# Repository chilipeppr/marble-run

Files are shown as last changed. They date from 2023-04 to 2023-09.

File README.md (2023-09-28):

# Liberty Christian School - Strive Center - Evolving Marble Run

Author: John Lauer

<i>This project was donated to the Liberty Christian School to inspire the kids to embrace today's modern tools to innovate for our future.</i>

This repo contains the following items:
- <b>Fusion 360 Marble Run Design</b> - The 3D design of the Marble Run that hangs on the wall
- <b>Fusion 360 PCB Board Design</b> - The 3D electronics design of the PCB that drives the Marble Run
- <b>3D Printer 3MF Files</b> - The 3MF 3D printable files for all of the parts

# Fusion 360 Marble Run Design

<table>
<tr><td>
The Marble Run hangs on a wall that is at least 8' high, although you could adjust the height in 80mm increments 
by just reducing how many "scoops" are on the GT2 timing belt. 

The main parts of this design are:
- The top NEMA 23 stepper motor with GT2 timing belt gear and "popper outer" component that pops the marbles off the scoops and onto the track
- The bottom idler pulley, marble reservoir, agitator (to ensure marbles fill the loading pipe), and the loading pipe to the scoops.
- Track components including straight rails and 90 degree corner angle rails.

The idea for the Marble Run is to inspire the kids to print their own section of track, using any design they dream up, to contribute to getting the marble to roll all the way from the top of the elevator back to the reservoir at the bottom. This will requires hundreds of sections of track to loop around a column in the STEM lab. Kids will learn how to use CAD to design their track and how to 3D print.

You can view the Fusion 360 design in the Autodesk gallery online. https://a360.co/3HKXjhC

To print all of the parts of the Marble Run, you can view the Fusion 360 design and export each body as a 3MF. A directory of 3MF's is also made available in this repo.
</td>
<td width="200">
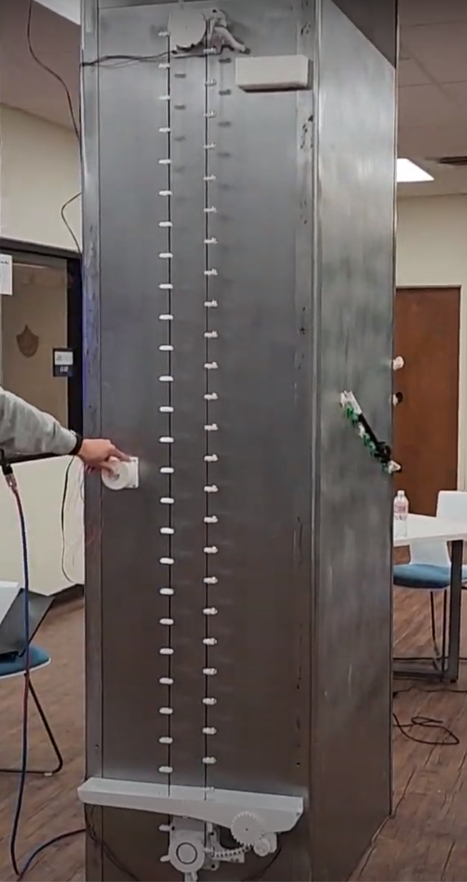
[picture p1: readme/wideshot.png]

</td>
</tr>
</table>

# Fusion 360 PCB Board Design

This is the driver board for the Marble Run. It has the following main modules:
- ESP32-S2 (Lolin S2 Mini)
- Stepper Motor TMC2209 Driver for Elevator
- Stepper Motor TMC2209 Driver for Agitator
- 2.42" OLED Display
- 24V to 5V DC to DC Converter
- 24V to 3.3V DC to DC Converter (Should have instead used AMS1117-3.3v off 5v bus)
- 24V Fan MOSFET Driver
- 24V Fan

You can view the board online in the Autodesk Gallery.
https://a360.co/3p5fhET

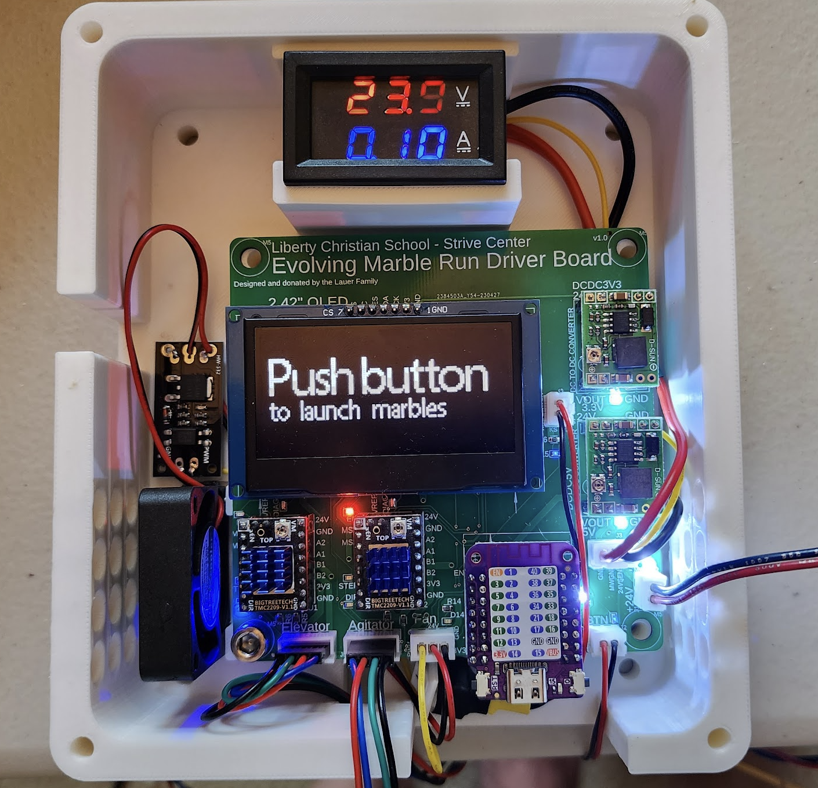
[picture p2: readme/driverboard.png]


This is a screenshot of what the PCB looks like inside Fusion 360.

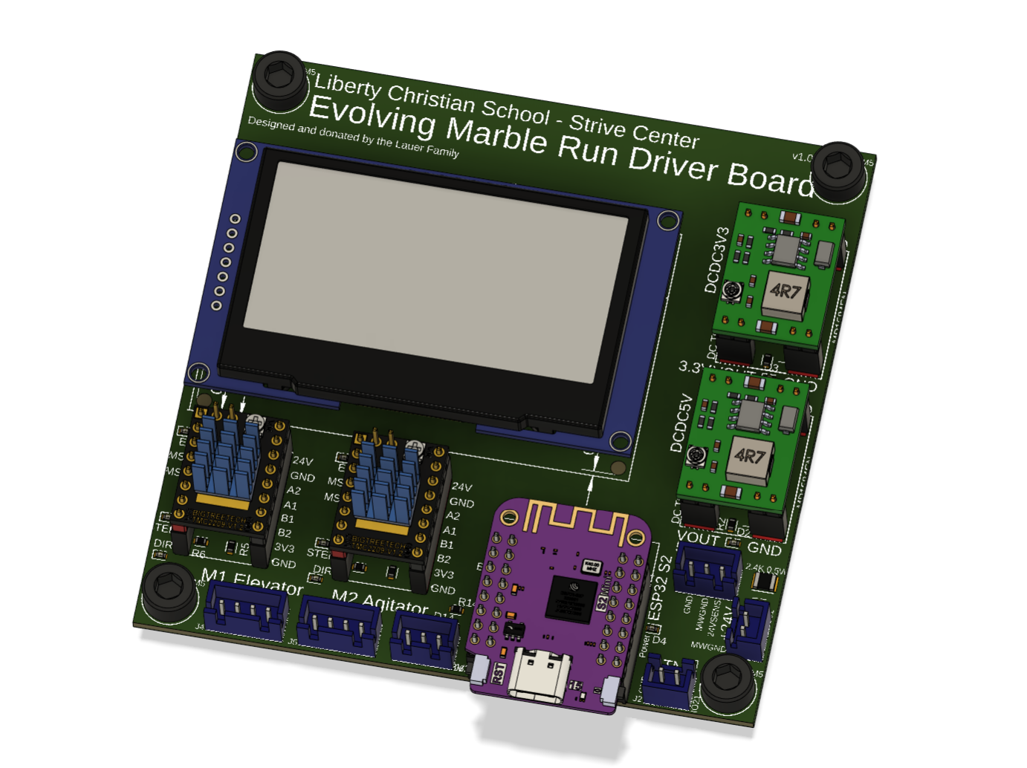
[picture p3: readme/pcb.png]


This is a preview of the board when ordering from JLCPCB including its placed components from their parts library.

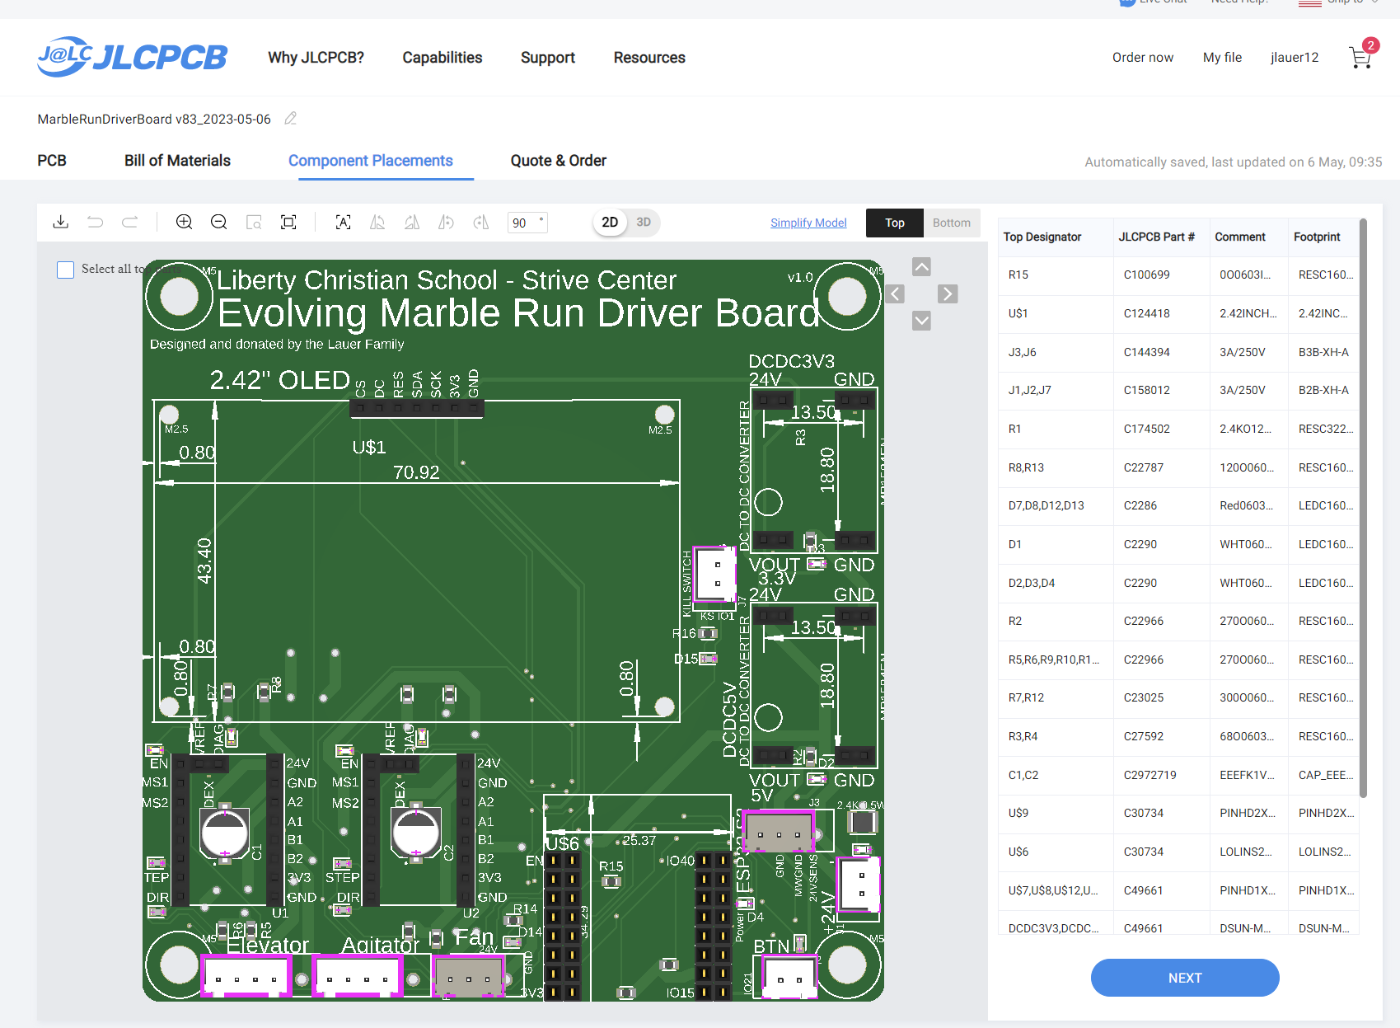
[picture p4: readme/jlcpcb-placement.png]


Here is a cost summary of the board.

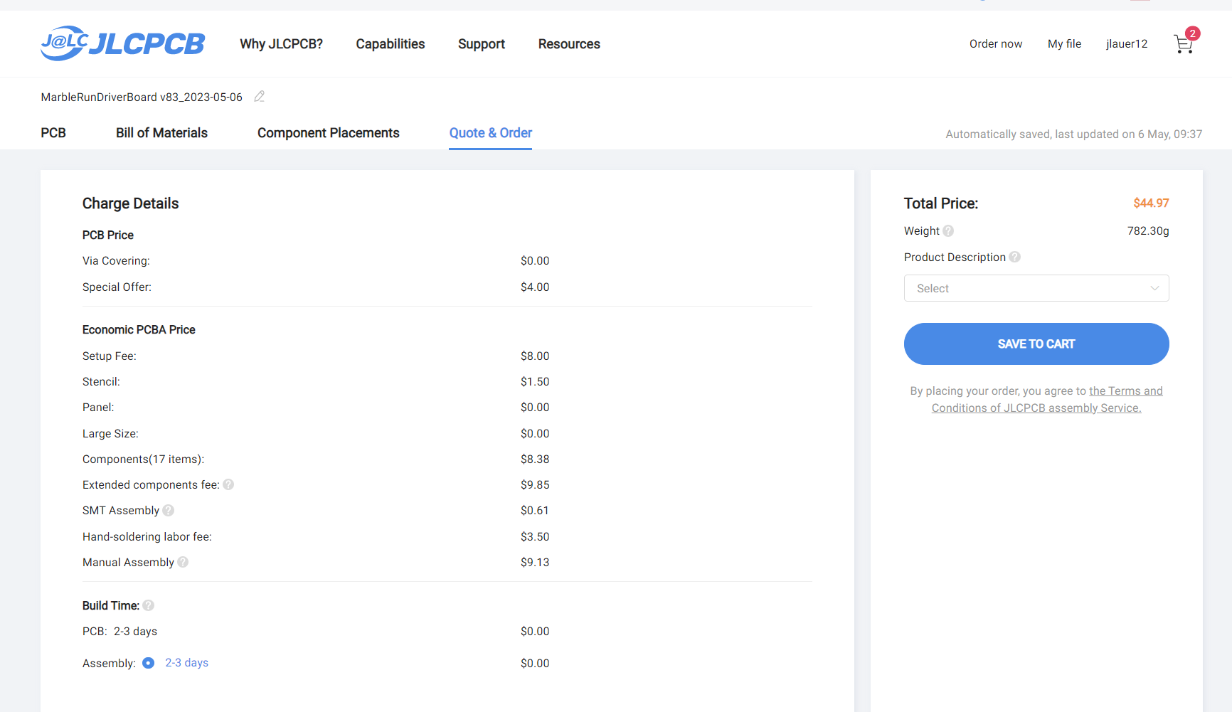
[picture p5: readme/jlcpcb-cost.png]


The code for running on an ESP32-S2 to control the Liberty Christian School Evolving Marble Run is available
in the "circuitpython 8.1.0 code" directory.

This is the board mocked up on a breadboard first before creating the final PCB.

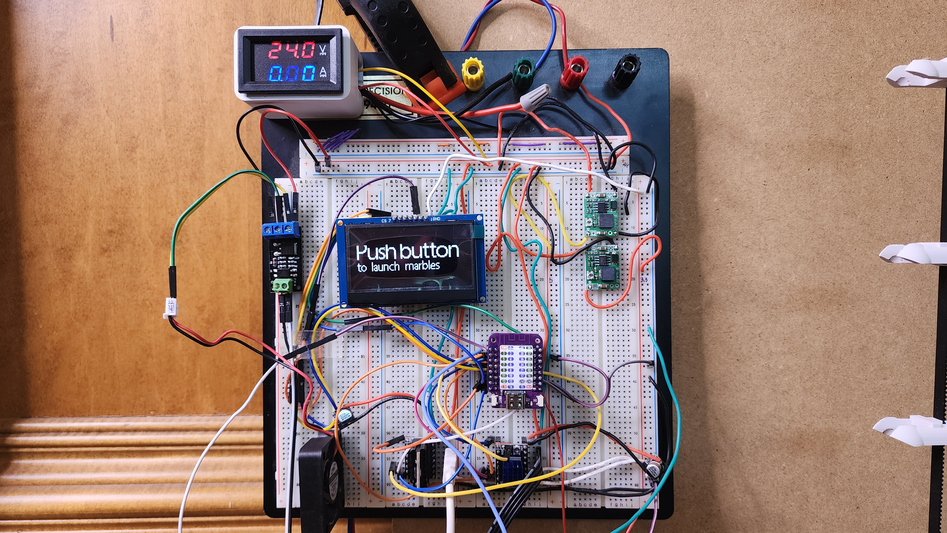
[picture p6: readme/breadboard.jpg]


# Schematic



















# Details of the Marble Run Components

This is a full view of the 8 foot tall Marble Run elevator that carries marbles from the bottom reservoir to the top of the run. This was mocked up prior to installing in the lab.

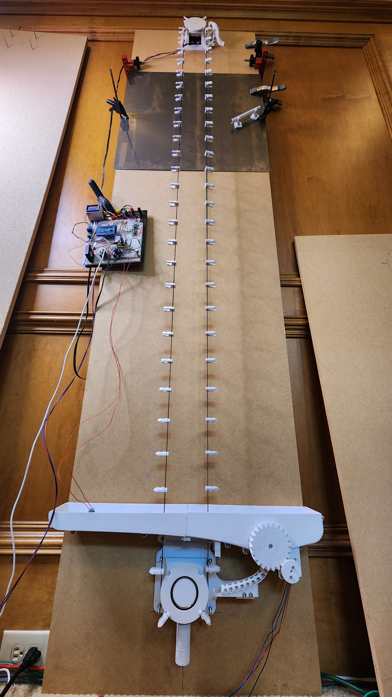
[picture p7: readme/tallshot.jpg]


This is a 3D rendering of the Marble Run. It was designed in CAD first to get all of the parts correct.

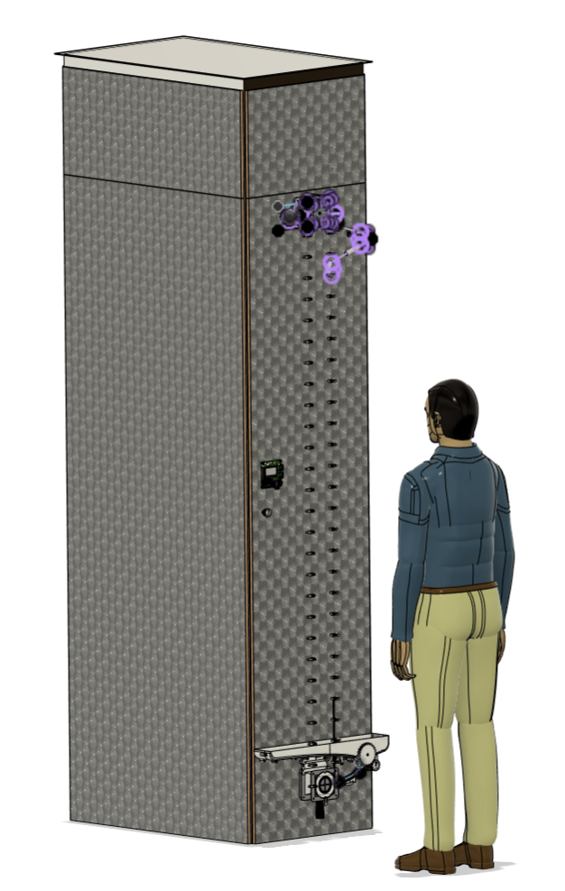
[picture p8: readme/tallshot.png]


This is the bottom reservoir. It has an agitator to ensure marbles are continuallyl flowing into the exit pipe, thus
ensuring the elevator is constantly picking up a new marble.

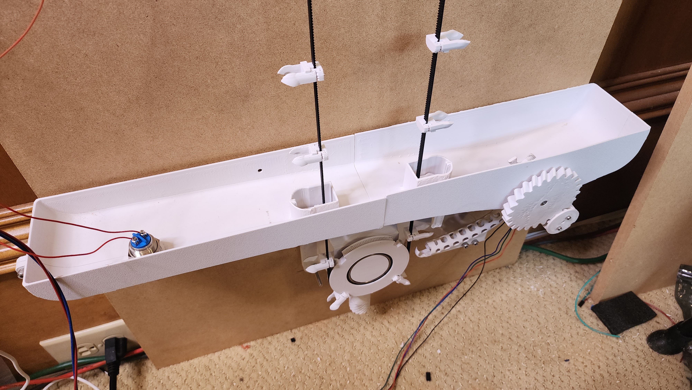
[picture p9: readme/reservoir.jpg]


This is the 3D rendering of the bottom reservoir.

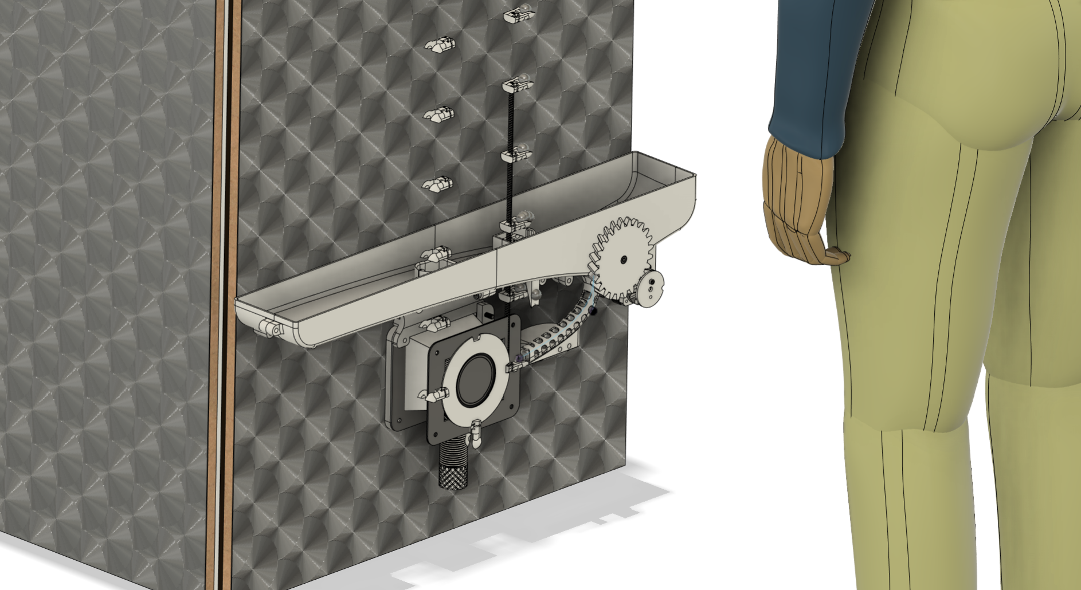
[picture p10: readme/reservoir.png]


This is the motor at top which rotates the GT2 timing belt. It is a NEMA 23 stepper motor.

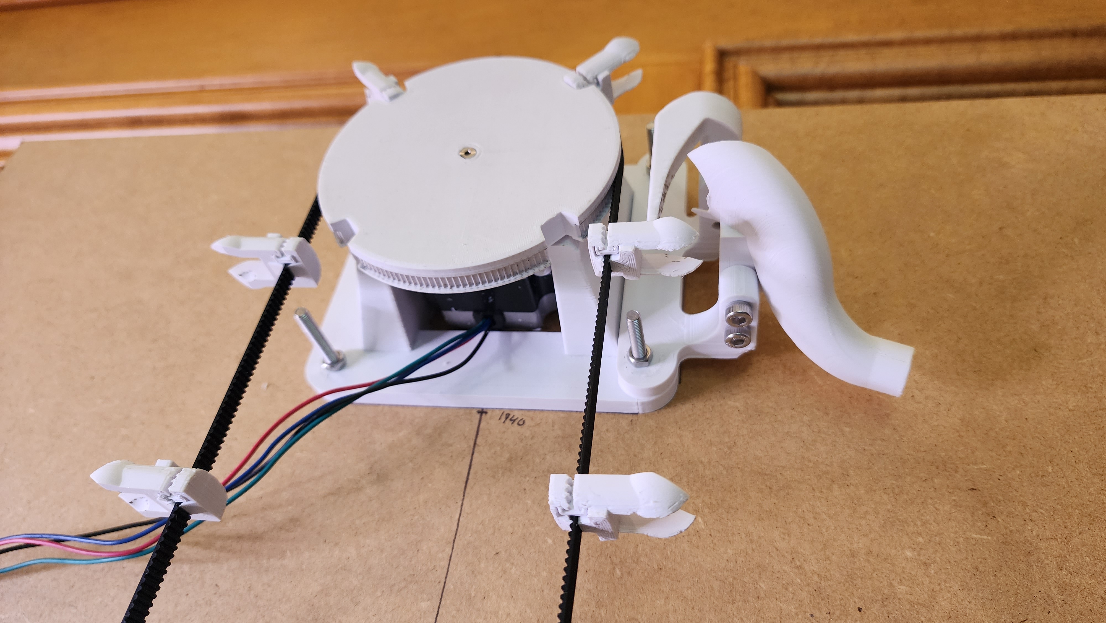
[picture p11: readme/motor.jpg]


This is the 3D rendering of the motor.
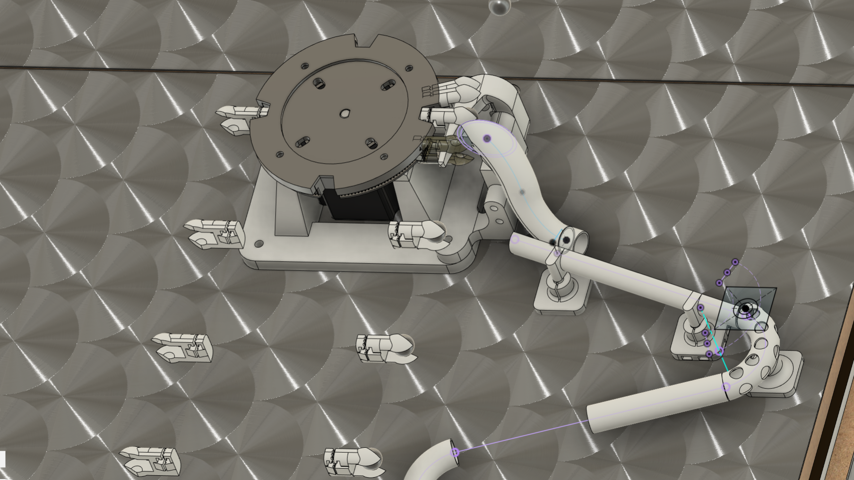
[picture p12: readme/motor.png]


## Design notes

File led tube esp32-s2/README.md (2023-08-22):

# LED Light Up Tube for Liberty Christian School Marble Run

This folder contains the CAD and circuitpython source code to build the
Light Up LED Tube running an ESP32-S2 mini to control 14 touch sensors.

The sensors trigger 28 WS2812 LED's with 2 LED's paired to each touch sensor.
As the stainless steel marble rolls across a wire embedded in the tube, it 
triggers the touch sensor which illuminates 2 LED's at full blue brightness
the moment it's touched.

Then a loop slowly fades the blue color as time progresses. Since the marble
triggers each touch sensor a fraction of a second after the prior one, you
get a rolling effect across the LED's as they match the rolling speed of
the marble.

There is also a 24v to 5v DC to DC converter used in the circuit so that
you can power the LED tube from the 24v wire that runs along the marble run
track. New wall magnet brackets were designed to accomodate the 24v wire.

This is a photo of the LED Tube hanging on the metal wall plate with magnets. It's lit up at 5% level of blue
on the LED's during idle to indicate it's on and ready for a marble to roll through it.

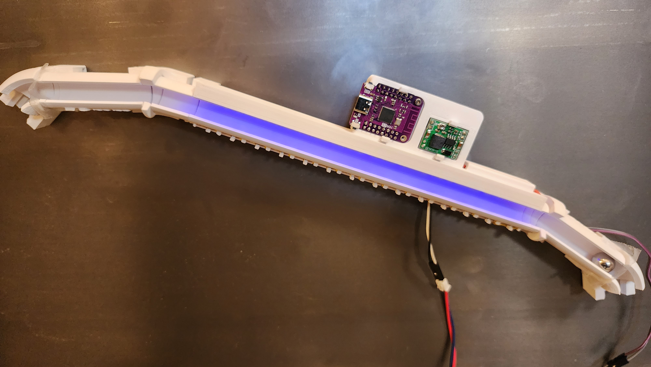
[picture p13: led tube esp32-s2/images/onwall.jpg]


Front photo of LED Tube

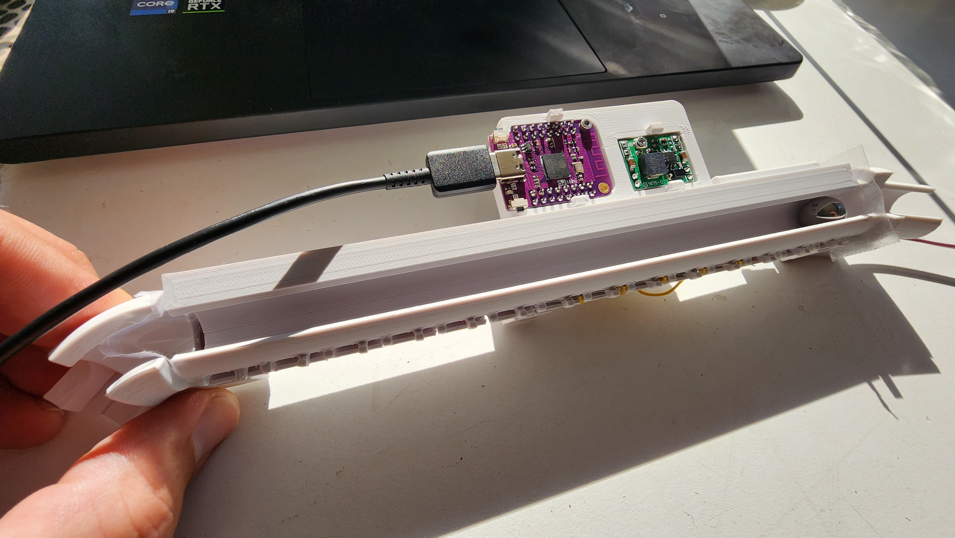
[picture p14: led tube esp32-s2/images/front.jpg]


Back photo of LED Tube

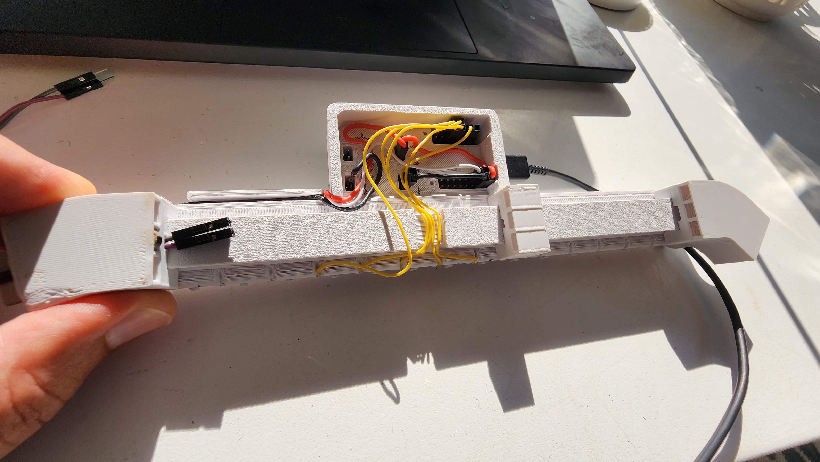
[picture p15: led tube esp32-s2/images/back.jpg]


The 14 touch wires run along the bottom of the tube and the stainless steel ball
bearing rolls over them to trigger a touch capacitance change on the ESP32 microcontroller.

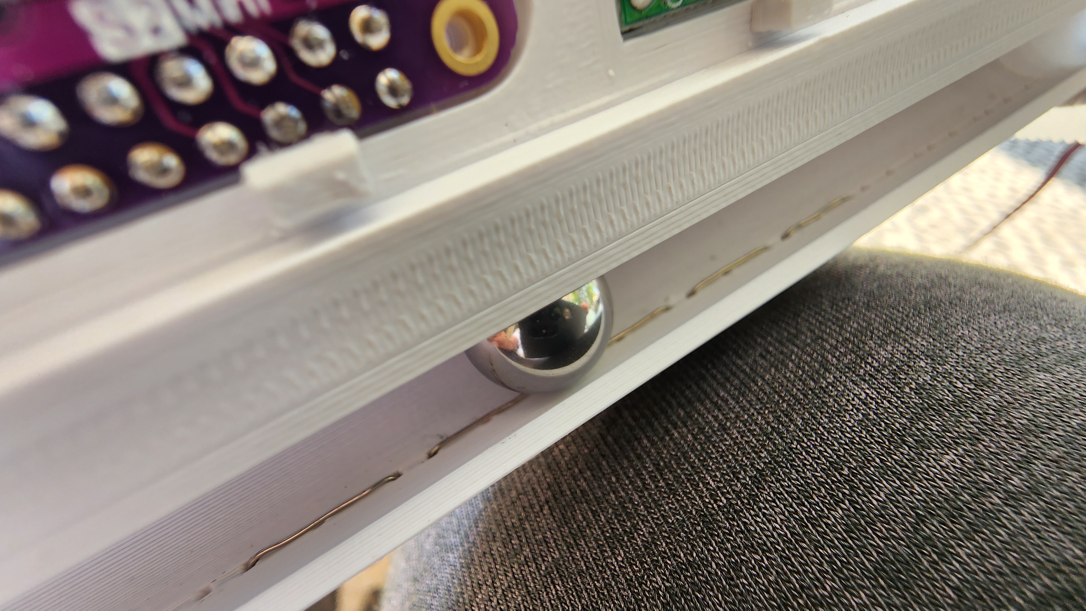
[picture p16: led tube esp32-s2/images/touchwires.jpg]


28 WS2812 RGB LEDs run along the top of the tube. They are controlled by one GPIO port on the
ESP32 which sends the color changing commands to the LED with a high refresh rate to create
the animations of the LEDs as the marble rolls along the track.

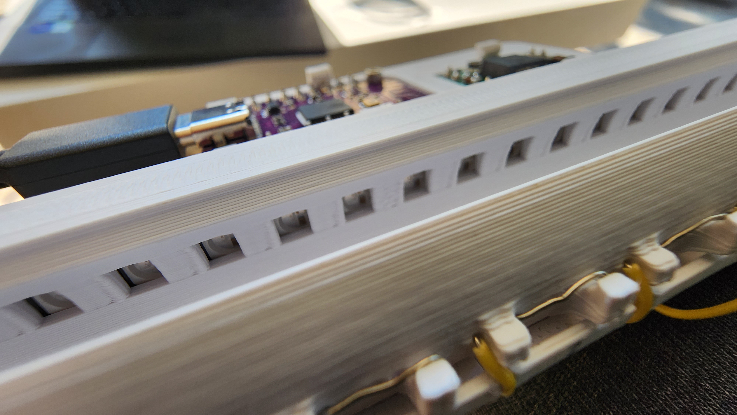
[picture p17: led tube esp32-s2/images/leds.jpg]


Wires are run along the bottom of the tube and into the ESP32 into their appropriate GPIO ports.

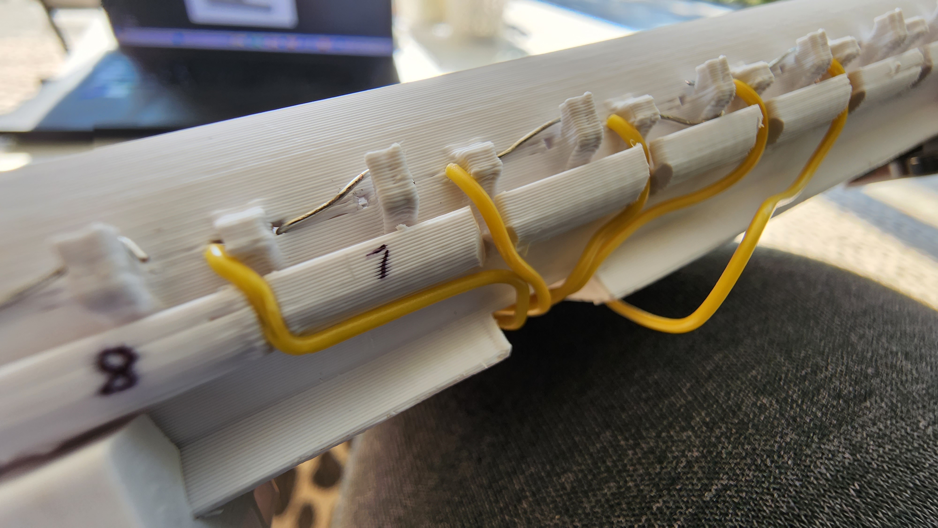
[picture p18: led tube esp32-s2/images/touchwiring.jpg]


The wiring on the back of the ESP32

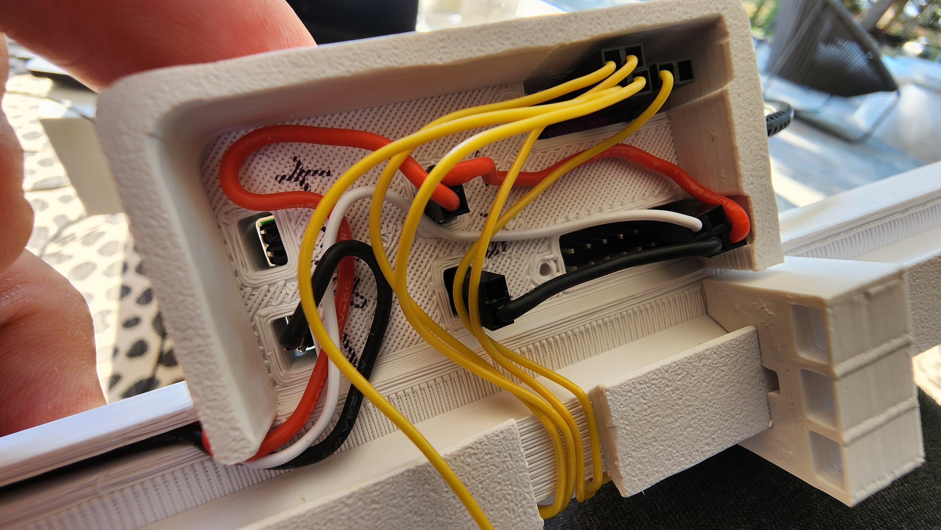
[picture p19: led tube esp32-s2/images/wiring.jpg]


Front angle 1 CAD rendering of LED Tube

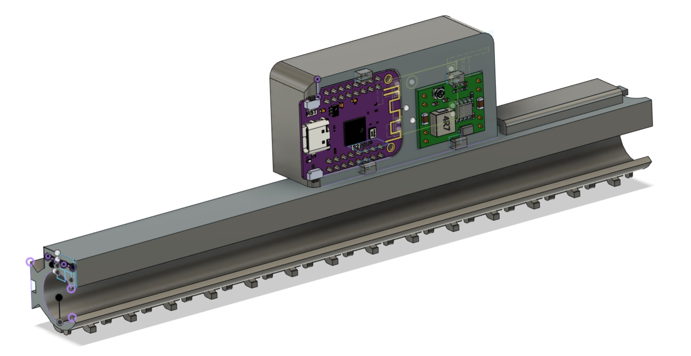
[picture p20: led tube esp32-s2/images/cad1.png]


Front angle 2 CAD rendering of LED Tube

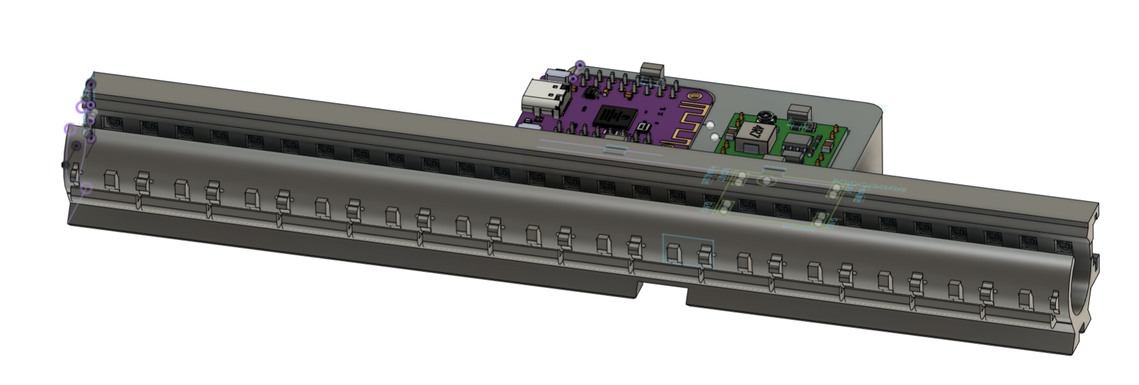
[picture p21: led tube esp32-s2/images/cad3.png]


Back angle CAD rendering of LED Tube

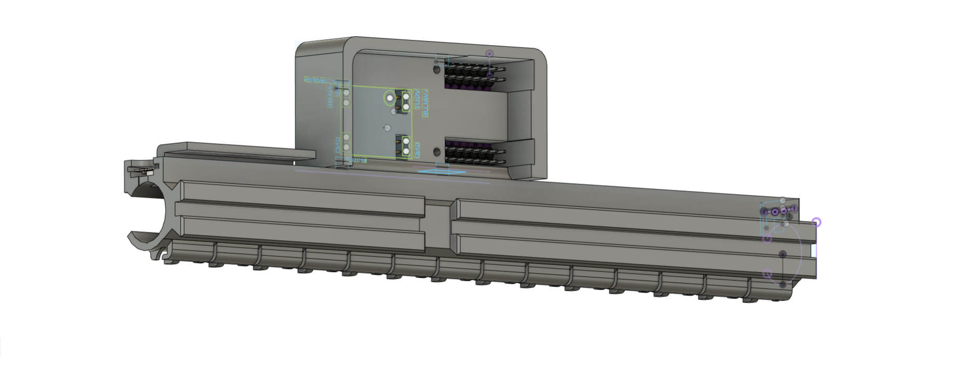
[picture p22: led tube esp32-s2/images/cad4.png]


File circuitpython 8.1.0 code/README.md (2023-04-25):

# marble-run
The code for running on an ESP32-S2 to control the Liberty Christian School Evolving Marble Run

This is the prototype breadboard for driving the Marble Run. It has the following main modules:
- ESP32-S2 (Lolin S2 Mini)
- Stepper Motor TMC2209 Driver for Elevator
- Stepper Motor TMC2209 Driver for Agitator
- 2.42" OLED Display
- 24V to 5V DC to DC Converter
- 24V to 3.3V DC to DC Converter
- 24V Fan MOSFET Driver
- 24V Fan

<>

PCB designed in Fusion 360 Electronics and produced at JLCPCB.
<>

This is a full view of the 8 foot tall Marble Run elevator that carries marbles from the bottom reservoir to the top of the run.
<>
<>

This is the bottom reservoir. It has an agitator to ensure marbles are continuallyl flowing into the exit pipe, thus
ensuring the elevator is constantly picking up a new marble.
<>
<>

This is the motor at top which rotates the GT2 timing belt. It is a NEMA 23 stepper motor.
<>
<>

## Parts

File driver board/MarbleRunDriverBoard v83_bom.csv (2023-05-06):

Comment | Designator | Footprint | LCSC Part #
0O 0603 IO4 to IO7 loopback | R15 | RESC1608X60 | C100699
2.4KO 1210 0.5W 9mA 194.4mW | R1 | RESC3224X71 | C174502
2.42INCHOLED | U$1 | 2.42INCHOLED | C124418
3A/250V | J1 J2 J7 | B2B-XH-A | C158012
3A/250V | J3 J6 | B3B-XH-A | C144394
3A/250V | J4 J5 | B4B-XH-A | C5341203
68O 0603 100mW 8ma 4.352mw | R3 R4 | RESC1608X60 | C27592
120O 0603 100mW 10ma 12mw | R8 R13 | RESC1608X60 | C22787
270O 0603 100mW 2ma 1.08mw | R5 R6 R9 R10 R11 R14 R16 | RESC1608X60 | C22966
270O 0603 100mW 9ma 21.87mw | R2 | RESC1608X60 | C22966
300O 0603 100mW 4ma 4.8mw | R7 R12 | RESC1608X60 | C23025
Blue 0603 10ma 2.8vF | D5 D6 D9 D10 D11 D14 D15 | LEDC1608X80N_FLAT-Y | C72041
DSUN-MP1584EN | DCDC3V3 DCDC5V | DSUN-MP1584EN | C49661
EEEFK1V101XP | C1 C2 | CAP_EEEFK1V101XP | C2972719
LOLINS2MINI | U$6 | LOLINS2MINI | C30734
PINHD1X2_GHOST | U$7 U$8 U$12 U$13 U$14 U$15 U$16 U$17 | PINHD1X2_GHOST | C49661
PINHD1X8_GHOST | U$10 U$11 | PINHD1X8_GHOST | C5224027
PINHD2X8_GHOST | U$9 | PINHD2X8_GHOST | C30734
Red 0603 20ma 2.1vF | D7 D8 D12 D13 | LEDC1608X80N_FLAT-Y | C2286
TMC2209_SILENTSTEPSTICK | U1 U2 | TMC2209_SILENTSTEPSTICK | C5224027
WHT 0603 10ma 2.8vF | D2 D3 D4 | LEDC1608X80N_FLAT-Y | C2290
WHT 0603 20ma 2.8vF | D1 | LEDC1608X80N_FLAT-Y | C2290

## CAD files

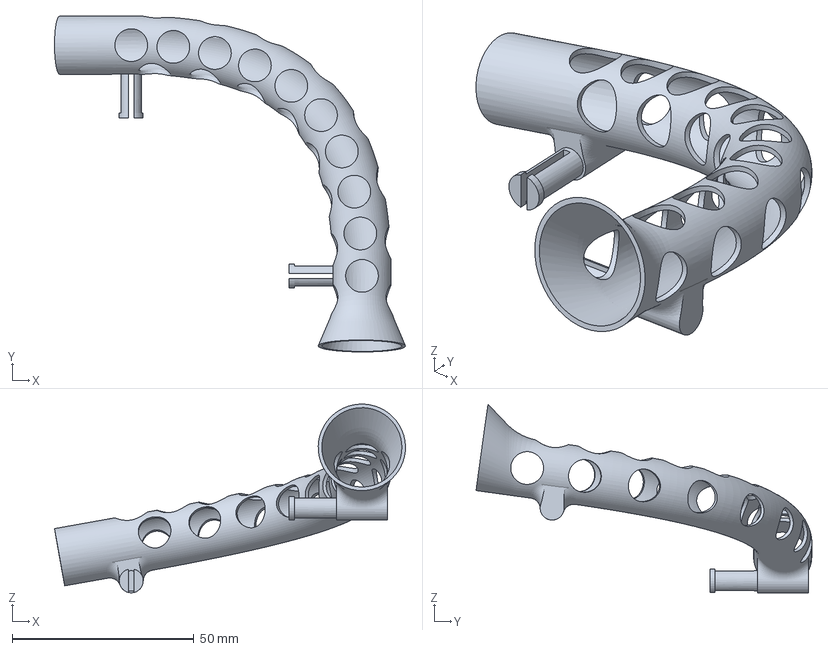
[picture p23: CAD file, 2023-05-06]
3mfs/CornerPipe.3mf
96.5 x 92.3 x 51.9 mm

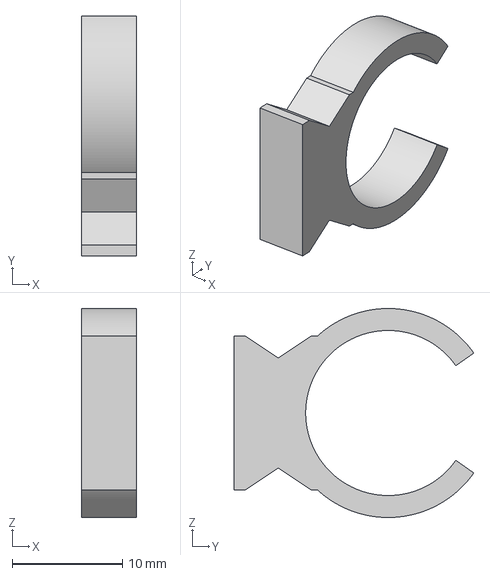
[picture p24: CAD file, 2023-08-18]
3mfsAug18_2023/Tube5mm.3mf
5.00 x 21.8 x 19.0 mm

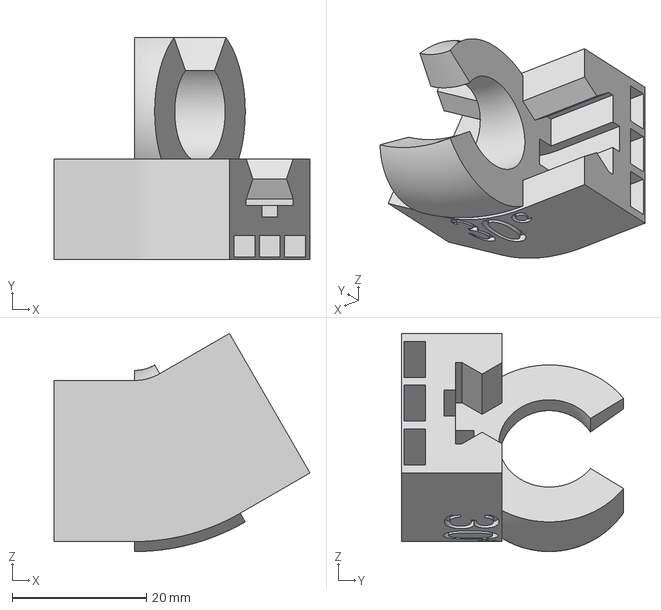
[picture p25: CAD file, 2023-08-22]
3mfsAug21_2023/BracketToWall30Deg.3mf
38.1 x 33.1 x 32.5 mm

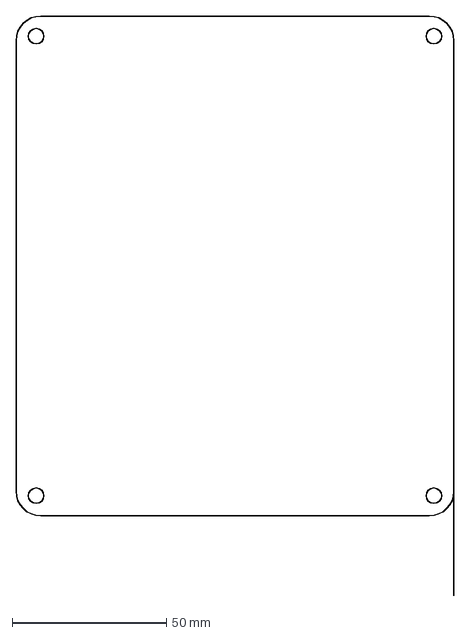
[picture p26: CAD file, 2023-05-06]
fusion360/AcrylicFrontCoverOfPCBBox_LaserCut.dxf
142.0 x 188.0 mm

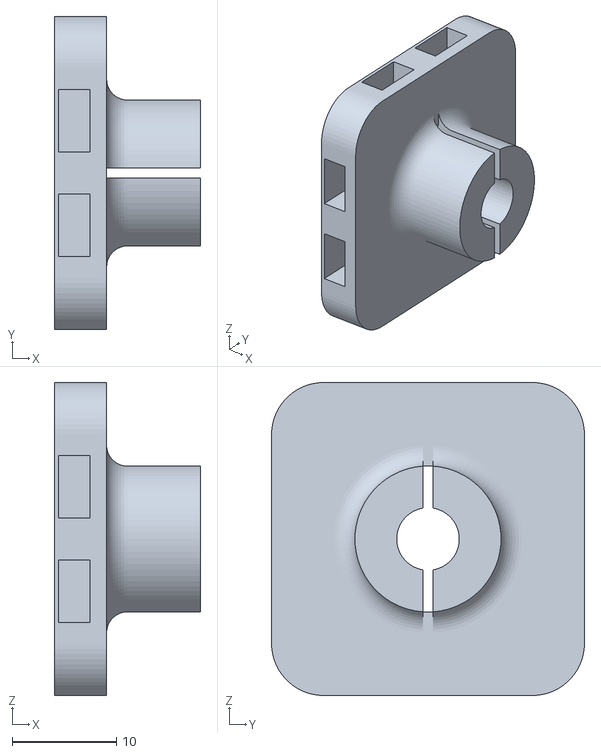
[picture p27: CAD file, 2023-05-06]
3mfs/HalfPipeWallBracketMagnet (2).stl
14.0 x 30.0 x 30.0

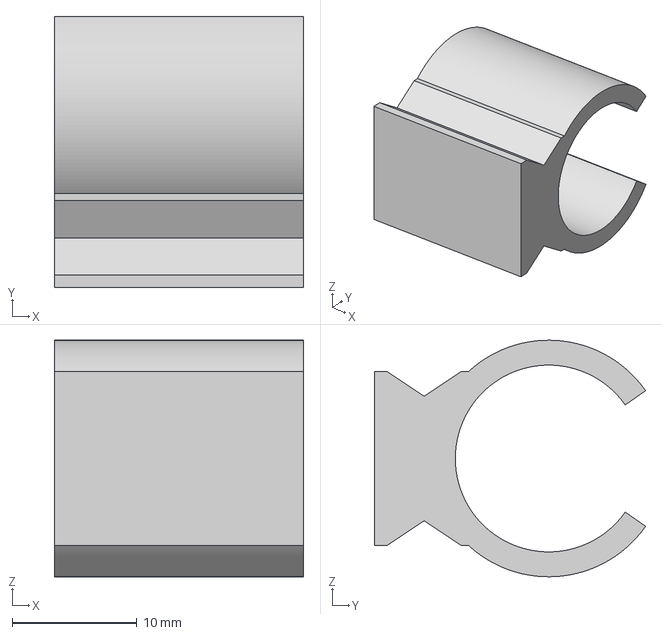
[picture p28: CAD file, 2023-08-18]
3mfsAug18_2023/Tube20mm.3mf
20.0 x 21.8 x 19.0 mm

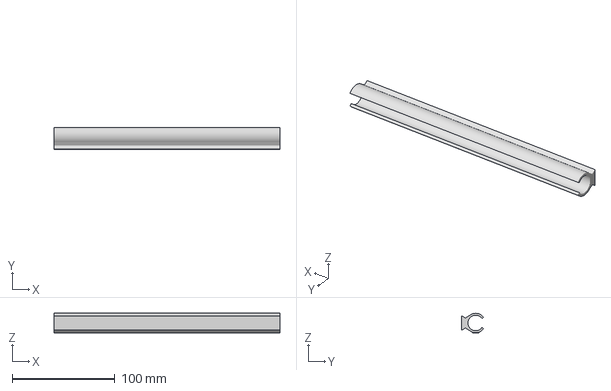
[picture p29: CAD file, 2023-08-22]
3mfsAug21_2023/Tube220mm.3mf
220.0 x 21.8 x 19.0 mm

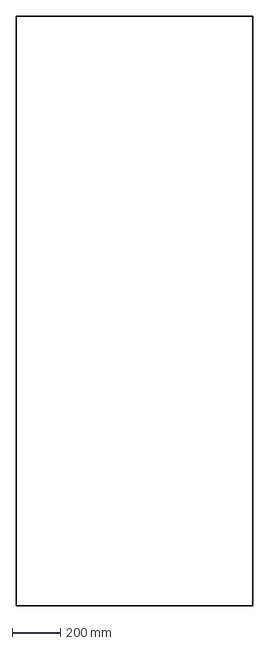
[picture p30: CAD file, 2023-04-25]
fusion360/EastWestLargeMetalSheet.dxf
977.9 x 2438.4 mm

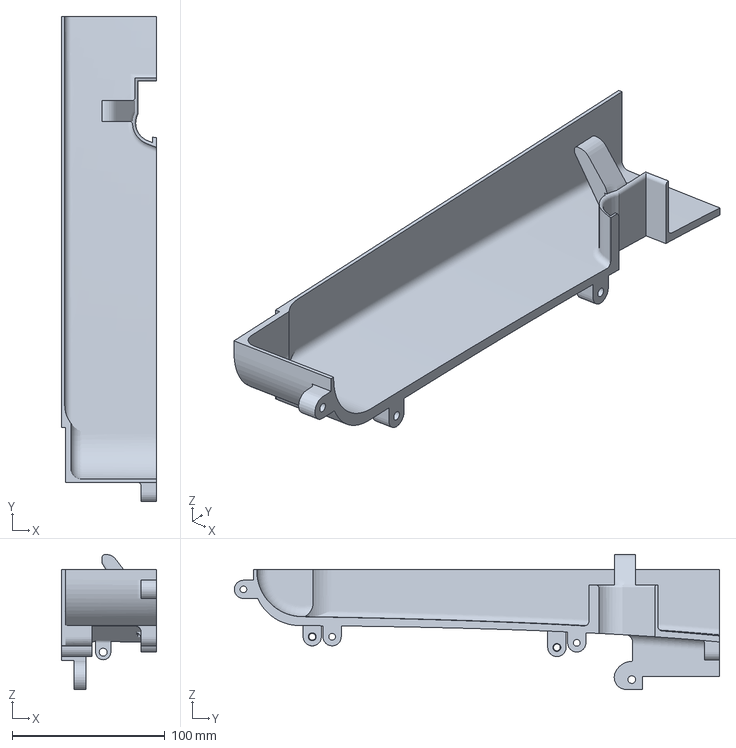
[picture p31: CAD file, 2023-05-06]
3mfs/Reservoir.3mf
62.0 x 317.5 x 88.3 mm

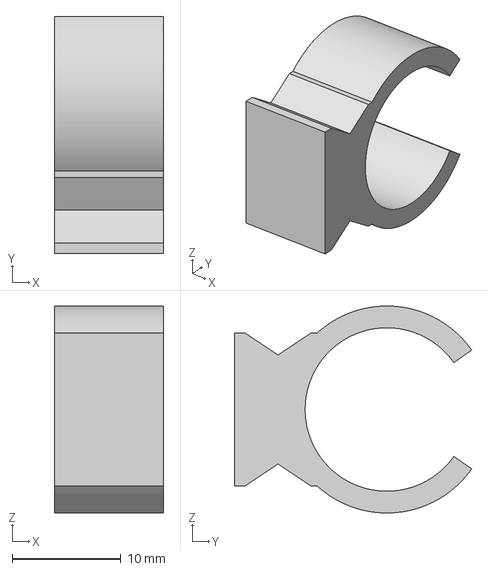
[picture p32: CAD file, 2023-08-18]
3mfsAug18_2023/Tube10mm.3mf
10.0 x 21.8 x 19.0 mm

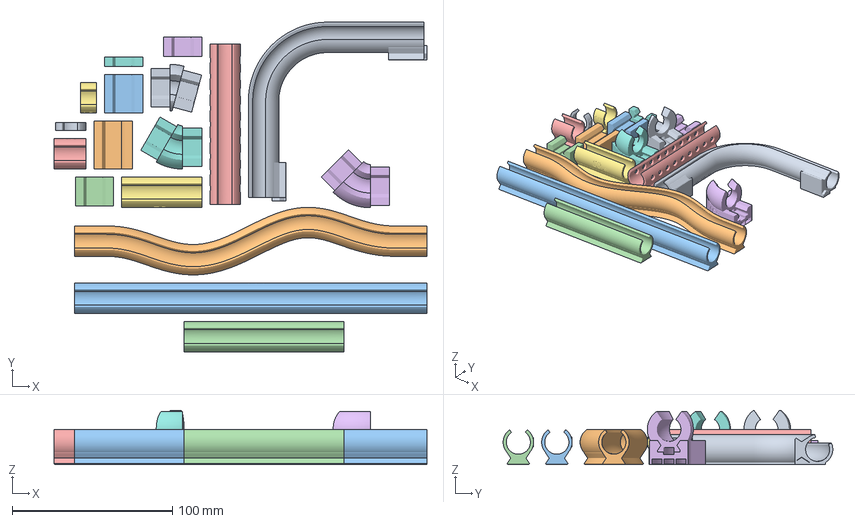
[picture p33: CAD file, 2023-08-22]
3mfsAug21_2023/Bambu_NewTubesAug21_2023.3mf
232.8 x 205.7 x 33.9 mm
NewTubesAug21_2023.3mf(8)
NewTubesAug21_2023.3mf(9)
NewTubesAug21_2023.3mf(14)
NewTubesAug21_2023.3mf(10)
NewTubesAug21_2023.3mf(11)
NewTubesAug21_2023.3mf(5)
NewTubesAug21_2023.3mf(15)
NewTubesAug21_2023.3mf(3)
NewTubesAug21_2023.3mf(1)
NewTubesAug21_2023.3mf(2)
NewTubesAug21_2023.3mf
NewTubesAug21_2023.3mf(7)
NewTubesAug21_2023.3mf(13)
NewTubesAug21_2023.3mf(6)
NewTubesAug21_2023.3mf(12)
NewTubesAug21_2023.3mf(4)
NewTubesAug21_2023.3mf(16)

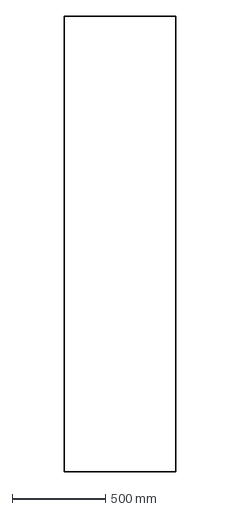
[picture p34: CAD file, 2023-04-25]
fusion360/NorthMetalSheet.dxf
596.9 x 2438.4 mm

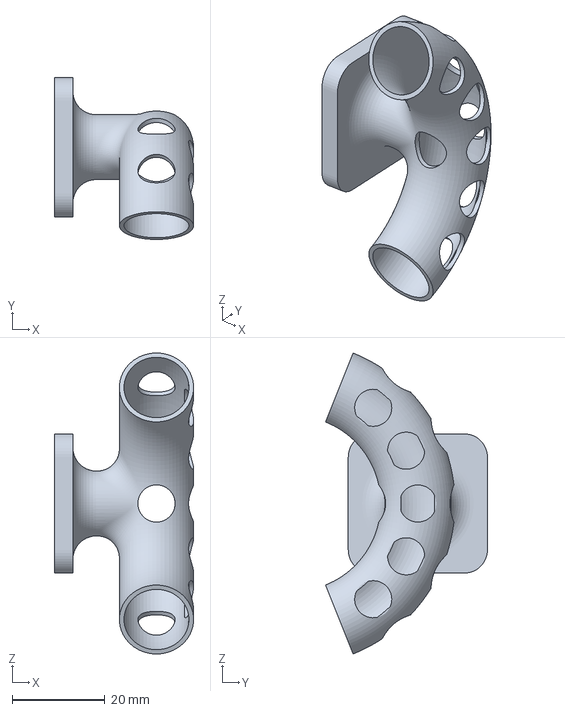
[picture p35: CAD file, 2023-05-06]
3mfs/136DegreeAngleWithWallBracket.3mf
30.0 x 34.9 x 64.9 mm

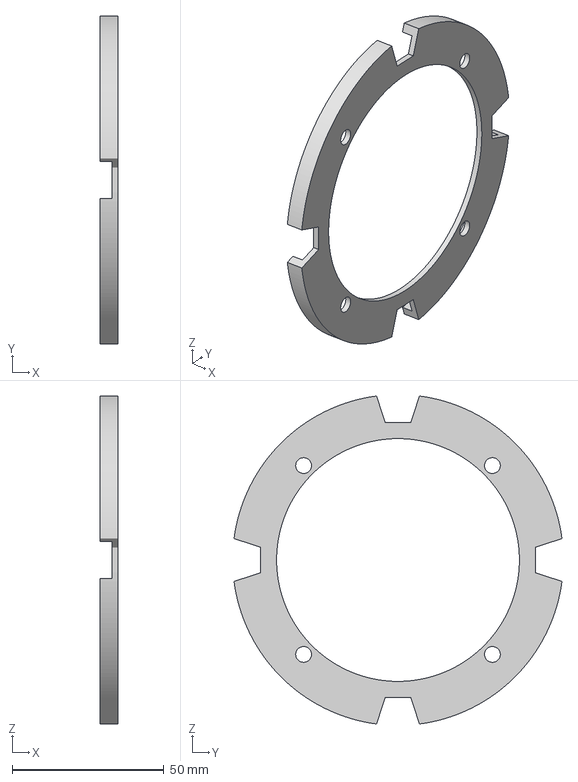
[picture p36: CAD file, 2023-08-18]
3mfsAug18_2023/TimingGearBeltHolderOnner.3mf
5.90 x 108.1 x 108.1 mm

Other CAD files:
3mfsAug21_2023/BracketToWall15Deg.3mf
fusion360/EastWestTopSmallMetalSheet.dxf
3mfs/HalfPipe165mmWithFunnelAtEntry_Bambu.3mf
3mfsAug18_2023/LittleWireBox.3mf
3mfs/1stAngleWithWallBracket.3mf
3mfs/1stGear10Teeth12mmWide.3mf
3mfs/1stGearCap.3mf
3mfs/2ndGear18Teeth12mmWide.3mf
3mfs/2ndGearInnerAxleCap.3mf
3mfs/2ndGearOuterCap.3mf
3mfs/BottomIdlerPulleyTemplate.3mf
3mfs/BracketAndReservoir.3mf
3mfs/BracketToBracket.3mf
3mfs/BracketToPushBeltBackOnTrack.3mf
3mfs/BracketToSteepPipe.3mf
3mfs/BtnHolder.3mf
3mfs/CaseForVoltAmmeter.3mf
3mfs/CatcherTo20mmWallOffset.3mf
3mfs/Clip.3mf
3mfs/Clipv2.3mf
3mfs/ContinuousFlapperStar.3mf
3mfs/CornerPipe.stl
3mfs/FlapperV2.3mf
3mfs/Gear24RWithShaft.3mf
3mfs/HalfPipe155mm.3mf
3mfs/HalfPipe165mmWithFunnelAtEntry.3mf
3mfs/HalfPipe165mmWithFunnelAtEntry.stl
3mfs/HalfPipeWallBracket.3mf
3mfs/HalfPipeWallBracketMagnet.3mf
3mfs/IdlerBearingInner.3mf
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

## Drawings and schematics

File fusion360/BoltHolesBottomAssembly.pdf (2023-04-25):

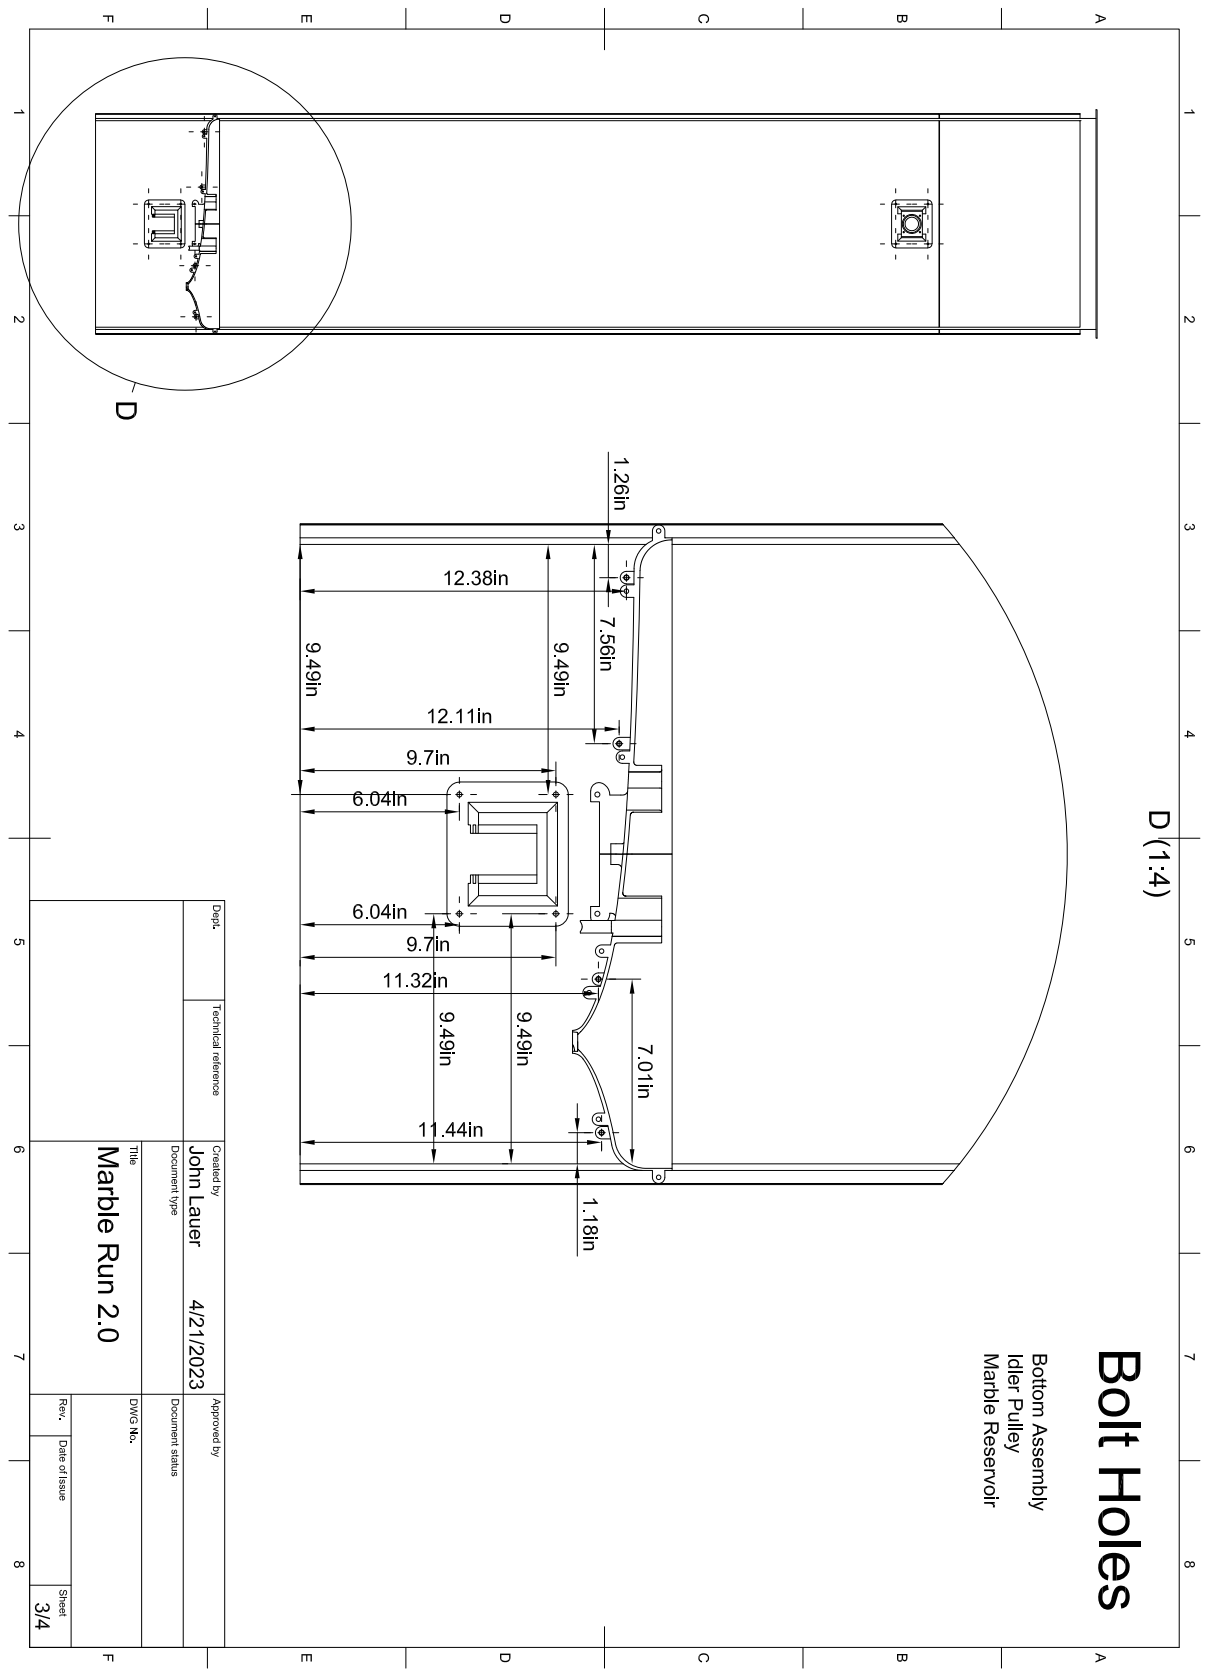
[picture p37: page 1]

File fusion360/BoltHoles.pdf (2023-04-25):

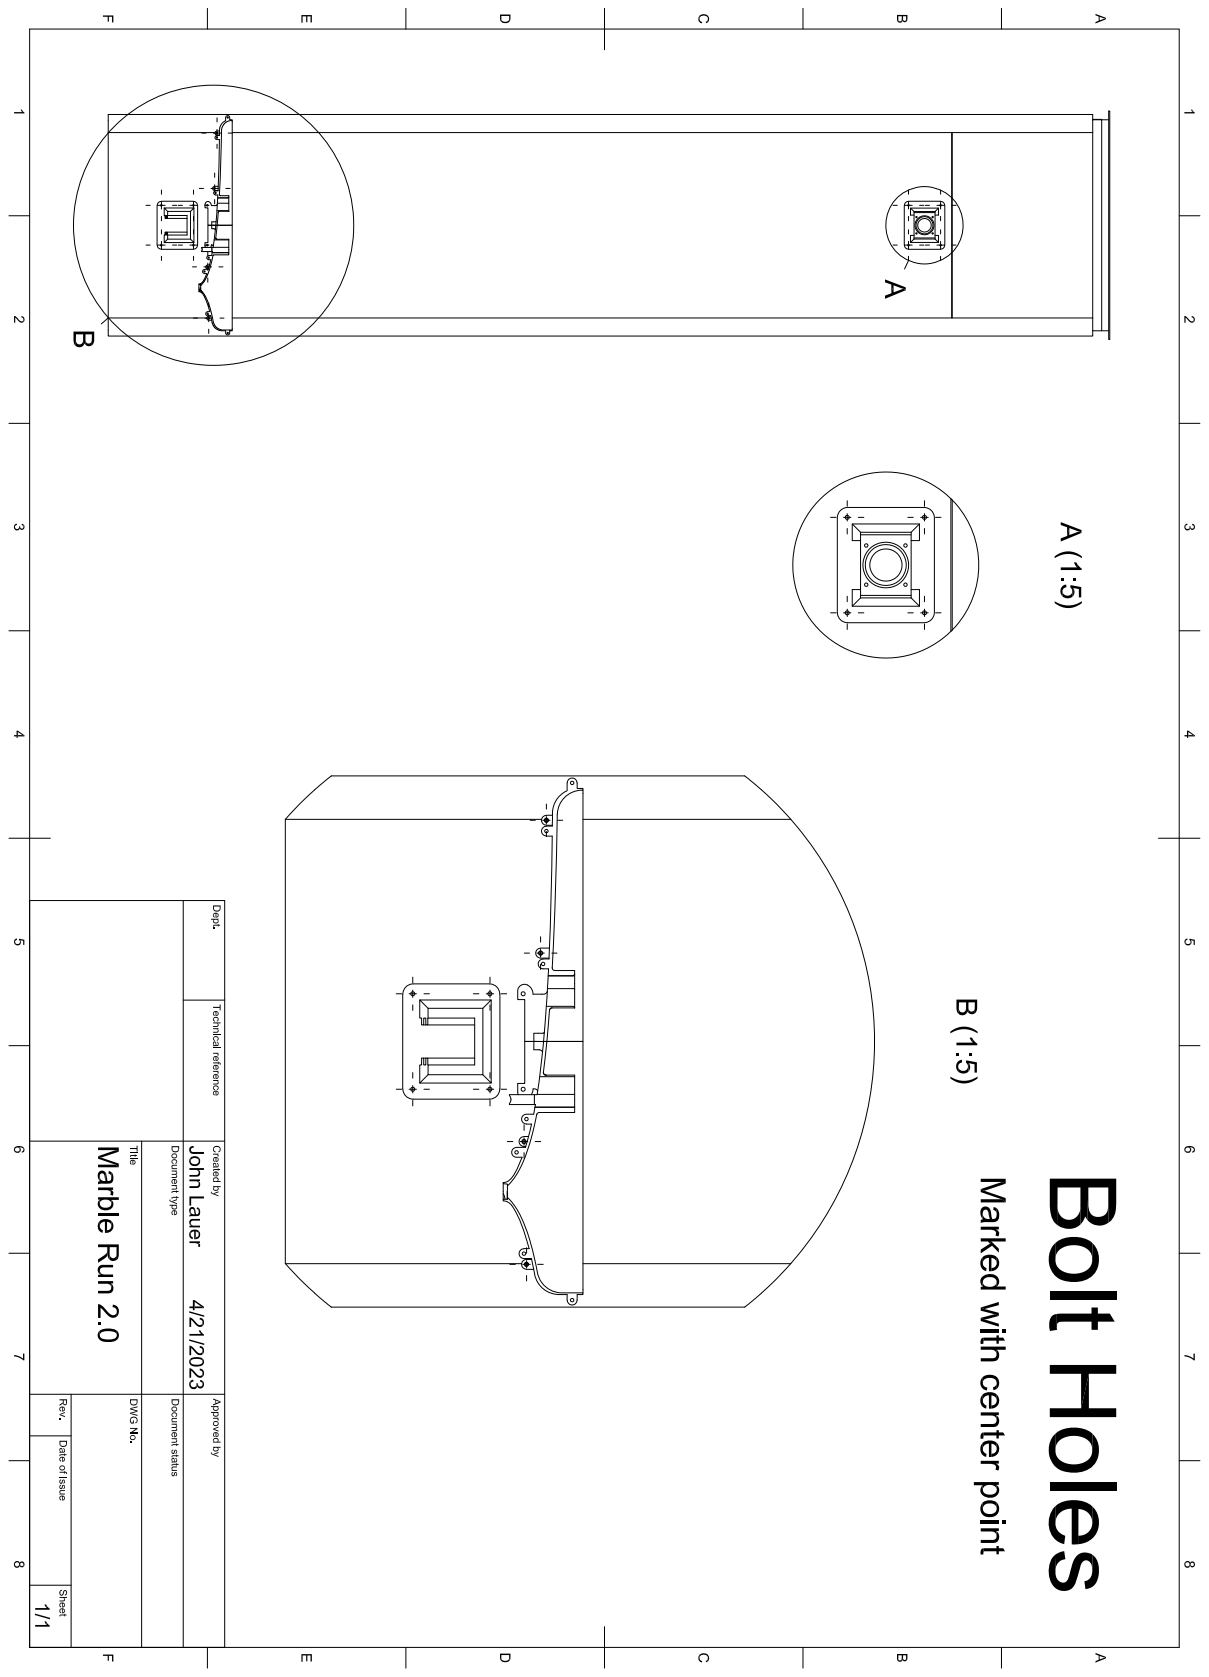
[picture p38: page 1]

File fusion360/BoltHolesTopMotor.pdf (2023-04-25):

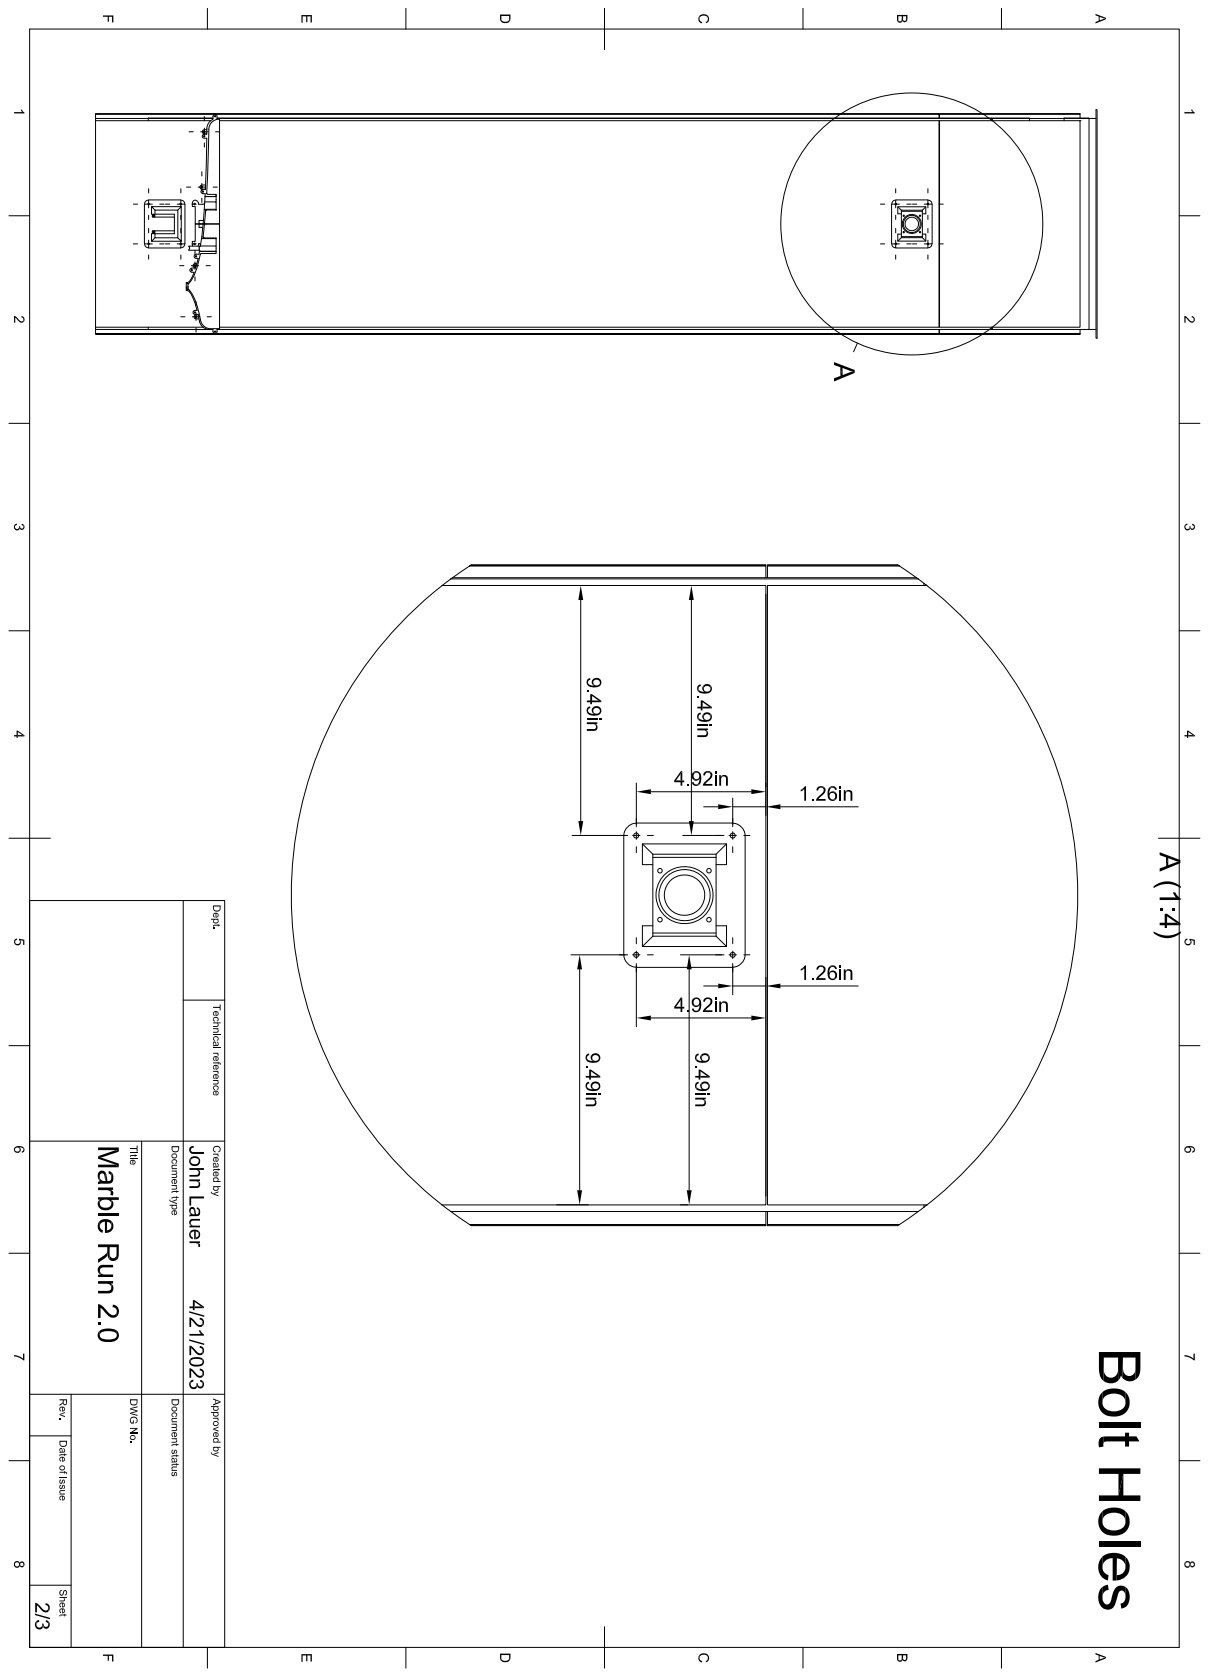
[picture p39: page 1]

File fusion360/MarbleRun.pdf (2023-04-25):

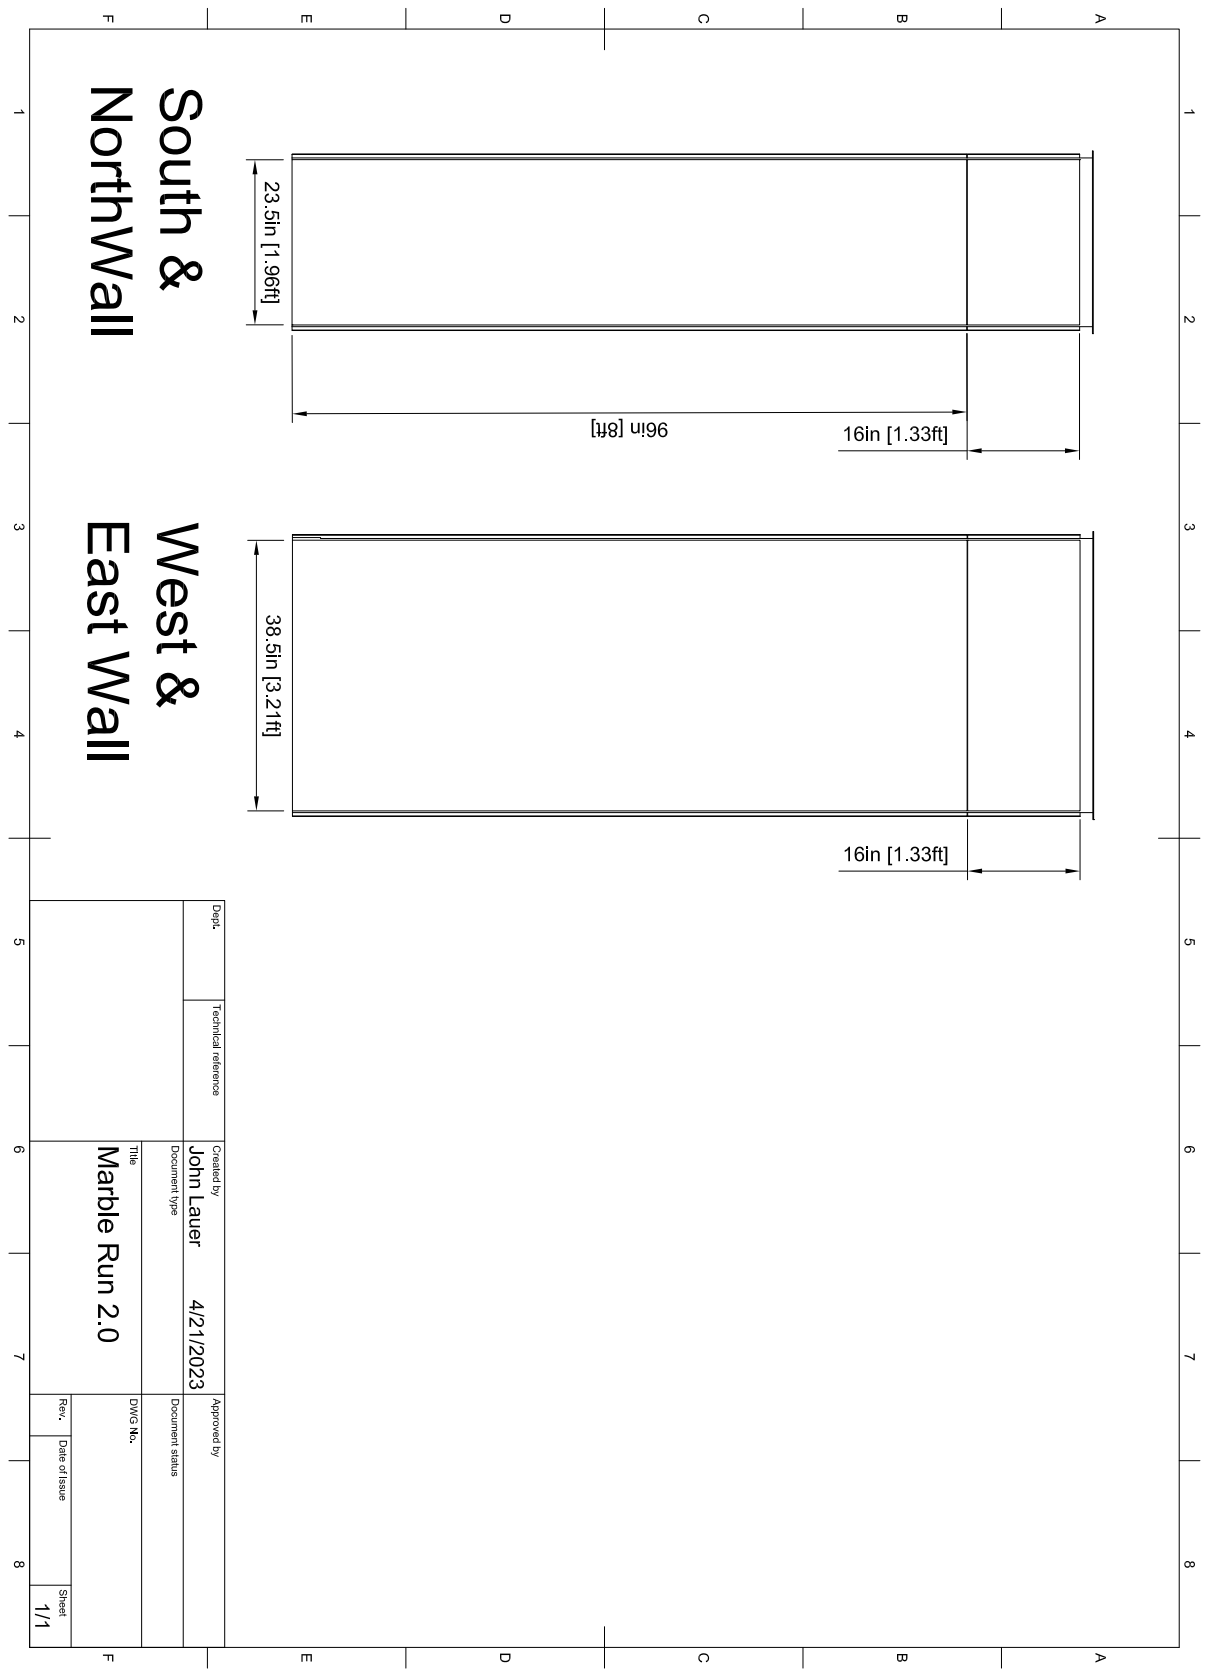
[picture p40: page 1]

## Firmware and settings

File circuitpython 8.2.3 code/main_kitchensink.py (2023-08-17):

# This file is the main entry point to the Marble Run
# It brings together the:
#   - Stepper Driver for the Elevator
#   - Stepper Driver for the Agitator
#   - Display
#   - Counter
#   - Button Listener
#   - Reboot Timer
#   - Fan

# import sys
# print("exiting immediately")
# sys.exit()

import asyncio
from button.button import Button 
# from button_mimic import ButtonMimic 
from stepper.stepper_tmc2209_pwm import Stepper
from stepper.stepper_tmc2209_pa_pwmagitator import StepperAgitator
import microcontroller
from display.display import Display
from display.display_bmp import DisplayBmp
from counter.counter import MarbleCounter
import board 
from fan.fan import Fan

""" 
PINS 

Elevator Stepper Motor
    In stepper/stepper_tmc2209_pwm.py

    self._pinEnablePin = board.IO5
    self._pinDirPin = board.IO6
    self._pinStepPin = board.IO7
    self._pinDiagPin = board.IO8
    # self._pinMs1Pin = board.IO9
    # self._pinMs2Pin = board.IO15

Agitator Stepper Motor
    In stepper/stepper_tmc2209_pa_pwmagitator.py

    self._pinEnablePin = board.IO13
    self._pinDirPin = board.IO14
    self._pinStepPin = board.IO15
    self._pinDiagPin = board.IO16
    # self._pinMs1Pin = board.IO9
    # self._pinMs2Pin = board.IO15

Display
    In display/display.py

    # On Teyleten  | GPIO for Lolin S2 Mini
    # SCK (SCLK)     IO12
    # SDA (MOSI)     IO11
    # RES (Reset)    IO9  
    # DC             IO38
    # CS (SS)        IO10

Loopback Step Counter
    In counter/counter.py

    # This pin should be loop connected to the step pin for the elevator
    # so connect it physically on the board to self._pinStepPin = board.IO7
    self.pinListenNum = board.IO4

Fan Control
    In fan/fan.py

    self.pinFanPwm = board.IO3

Button Listener
    In button/button.py

    self._pinButtonPin = board.IO21

Kill Switch Button
    In killswitch/killswitch.py
    
    self._pinKillSwitchPin = board.IO1
"""


class Dashboard:
    def __init__(self):

        print("Initting Dashboard")
        # self._pinButtonPin = board.IO21

        # BUTTON SETUP

        # Create an async button with callbacks for press/release
        self._button = Button(self.onPressCb, self.onReleaseCb)
        self.button_interrupt_task = asyncio.create_task(self._button.asyncTaskCatchButtonPinPress())

        # STEPPER MOTORS 

        # Create Elevator stepper object so we can call spin on button press/release
        self._stepper = Stepper(onAccelCb=self.onAccelCb, 
                                onMaxSpeedCb=self.onMaxCb, 
                                onDecelCb=self.onDecelCb,
                                onStoppedCb=self.onStoppedCb)
        # self._stepper.freqMax = 300
        # self._stepper.freqStep = 30
        # self._stepper.enable()

        # Create stepperAgitator object so we can call agitate on button press/release
        self._stepperAgitator = StepperAgitator()
        self._stepperAgitator.freqMax = 300
        self._stepperAgitator.freqStep = 40
        # self._stepperAgitator.enable()

        # Create spin task that spins the main motor to carry the marbles to the top
        # We need this as a task so that it can control the accel/decel on its own
        # We can just call start/stop on this task to have the motor accel/decel for us
        self.elevator_task = asyncio.create_task(self._stepper.spinAsyncTaskPwm())

        # Create a rocking agitator task that helps the marbles drop down
        # into the onramp pipe to the elevator
        # We can just call start/stop to have the rocking commence/end
        self.agitator_task = asyncio.create_task(self._stepperAgitator.spinAsyncTaskPwm())

        # DISPLAY AND MARBLE COUNTER

        # Create our display hardware object
        self.d = Display()

        # Create bitmap UI display helper object. Pass in display to init().
        self.dbmp = DisplayBmp(self.d.display)

        # Create our countio marble counting object. 
        # This counts steps on pin IO4, divides the steps to marble count, 
        # then calls our callback when appropriate.
        # Remember IO4 is physically wired to listen to IO7 to make this technique work
        # Pass in our callback to the init method that's called on each marble count update.
        self.mc = MarbleCounter(self.onMarbleCount)
        # self.mc.marbleCtr = 1073741700

        # Generate steps on IO7 as if user is pressing button to move steppers
        # Remember IO4 is physically wired to listen to IO7 to make this test frequency work
        # self.freqGen = self.turnOnTestFrequency()

        # Create the async task for our marble counter
        # This starts an infinite loop that counts the steps from the loopback pin 
        # and calls the callback when the count increases
        self.marble_count_task = asyncio.create_task(self.mc.asyncTaskCountSteps())

        # Create the async task that persists our marble count to disk so we can
        # keep track of it across reboots/crashes. It writes each hour.
        self.write_marblectr_todisk_task = asyncio.create_task(self.mc.asyncTaskWriteMarbleCountToDiskEveryHour())
        # self.mc.intervalSecsWriteMarbleCtrToDisk = 10 # temporarily override speed in seconds at which to write. defaults to 60*60 = 1 hr

        # Create the async task that shows the splash screens on the display
        self.display_task = asyncio.create_task(self.dbmp.asyncTaskShowSplashScreens())

        # FAN

        self.fan = Fan()
        self.fan.freqGen.frequency = 300
        self.fan.turnOff()

        # Create an async timer that reboots the ESP32-S2 every 8 hours
        # self.reboot_timer_task = asyncio.create_task(self.rebootTimer(60))  # 1 minute for testing
        self.reboot_timer_task = asyncio.create_task(self.rebootTimer(60*60*8)) # 8 hours
        # Manually log that we're rebooting
        from reboot.r import RebootReason
        self.rr = RebootReason()

        # Watch the wifi network
        from wifi.watcher import WifiWatcher
        ww = WifiWatcher()
        self.ww_task = asyncio.create_task(ww.asyncWifiWatcherTask())
        

    def deinit(self):
        self._stepper.disable()
        self._stepperAgitator.disable()

    def onPressCb(self):
        print("Got onPress. Spinning motor.")

        # Enable the power to the steppers
        # self._stepper.enable()
        self._stepperAgitator.enable()

        # start spinning
        self._stepper.spinAsyncStart()
        self._stepperAgitator.spinAsyncStart()

        # Turn on the fan to cool the stepper drivers
        self.fan.turnOn()

    def onReleaseCb(self):
        print("Got onRelease. Stopping motor.")
        # stop spinning
        self._stepper.spinAsyncStop()
        self._stepperAgitator.spinAsyncStop()
        # self._stepper.disable()

    def onMarbleCount(self, ctr):
        print("Got onMarbleCount. ctr:", ctr)

        # # for testing, let's show the info screen at increments
        # remainder = ctr % 30
        # if remainder >= 10 and remainder <= 15:
        #     self.dbmp.showAccel()

        # elif remainder >= 16 and remainder <= 20:
        #     self.dbmp.showMax()

        # elif remainder >= 21 and remainder <= 25:
        #     self.dbmp.showDecel()

        # elif remainder == 26:
        #     # this would be like our stepper object saying it's done showing info screens
        #     self.dbmp.showSplashScreensAgain()
            
        self.dbmp.updateCounter(ctr)

    def onAccelCb(self):
        # This is our callback we get from the elevator motor when it starts accelerating
        self.dbmp.showAccel()

    def onMaxCb(self):
        # This is our callback we get from the elevator motor when it is at max speed
        self.dbmp.showMax()

    def onDecelCb(self):
        # This is our callback we get from the elevator motor when it starts decelerating
        self.dbmp.showDecel()

    def onStoppedCb(self):
        # This is our callback we get from the elevator motor when it stops moving
        self.dbmp.showSplashScreensAgain()

        # Disable the hold power to the steppers
        # self._stepper.disable() # marbles will drop a bit
        self._stepperAgitator.disable()

        # Turn off fan
        self.fan.turnOff()

    async def rebootTimer(self, duration):
        print("Starting reboot timer. Duration (secs):", duration)
        
        await asyncio.sleep(duration) # don't forget the await
        
        self.rr.logToFileWithWifi("Manually rebooting due to reboot timer task")

        # Rebooting
        microcontroller.reset()

        print("Ended reboot timer")

async def main():
    
    d = Dashboard()

    # reboot_task = asyncio.create_task(d.rebootTimer(10))

    await asyncio.gather(
        d.marble_count_task, 
        d.display_task,
        d.write_marblectr_todisk_task, 
        d.button_interrupt_task, 
        d.elevator_task, 
        d.agitator_task,
        d.reboot_timer_task,
        d.ww_task
        )  # Don't forget the await!

    d.deinit()
    
    print("done with main")

asyncio.run(main())

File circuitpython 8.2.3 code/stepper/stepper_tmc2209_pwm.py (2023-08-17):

# The Liberty Christian Stepper Motor Library for CircuitPython
# This drives the main elevator stepper motor

import digitalio
import board
import time
import asyncio
import pwmio
# import enum

class StepperState():
    ACCELERATING = 1
    MAXSPEED = 2
    DECELERATING = 3
    STOPPED = 4

class Stepper:

    def __init__(self, onAccelCb=None, onMaxSpeedCb=None, onDecelCb=None, onStoppedCb=None):

        print("Initting Elevator Stepper library...")

        # Setup callbacks
        self.onAccelCb = onAccelCb
        self.onMaxSpeedCb = onMaxSpeedCb
        self.onDecelCb = onDecelCb
        self.onStoppedCb = onStoppedCb

        # Setup our state
        self.state = StepperState.STOPPED

        # Setup pins
        self._pinEnablePin = board.IO5
        self._pinDirPin = board.IO6
        self._pinStepPin = board.IO7
        self._pinDiagPin = board.IO8
        # self._pinMs1Pin = board.IO9
        # self._pinMs2Pin = board.IO15

        self._minPulseWidth = 0.001 #0.00055

        # open pins
        self._pinEnable = digitalio.DigitalInOut(self._pinEnablePin)
        self._pinEnable.direction = digitalio.Direction.OUTPUT
        self._pinDir = digitalio.DigitalInOut(self._pinDirPin)
        self._pinDir.direction = digitalio.Direction.OUTPUT
        # self._pinStep = digitalio.DigitalInOut(self._pinStepPin)
        # self._pinStep.direction = digitalio.Direction.OUTPUT
        self._pinDiag = digitalio.DigitalInOut(self._pinDiagPin)
        self._pinDiag.direction = digitalio.Direction.INPUT

        # setup pinStep as PWM output
        self.freqMin = 10   # we can't go below this (pwm hardware won't support it)
        # v2 has 3 gears: 10 teeth to 18 to 38, so 10/18 = 0.55 turns on gear 2 for 1 turn on gear 1 (the stepper motor)
        # then 18/38 for gear 2 to 3 is 0.47. so 0.55 * 0.47 = 0.26. so for 1 turn in we get a 1/4 turn out which is 4:1 reduction
        # so 300 rpm in v1 to have same speed in v2 is 300 * 4 = 1200
        self.freqMax = 1200 #1200 for v2 with gearing #300 for v1 with straight stepper rather than with gearing #700 #1000 # we can't go above as motor would turn too fast
        self.freqStep = 3 * 10 # since doing 0.1 sleep, if 0.01 sleep use 3  # when accel/decel on stepper this is the amount of ramp
        self._pinStep = pwmio.PWMOut(
            self._pinStepPin, 
            frequency=self.freqMax, # Not allowed to set to 0, so use duty_cycle as our method of turning off stepper
            duty_cycle=0, #2 ** 15,  # Cycles the pin with 50% duty cycle (half of 2 ** 16) 
            variable_frequency=True
            )
        # track our own frequency since the actual frequency of the pin ends up at a different number
        # than what we originally set it to, so our math gets screwed up unless we track on our own
        self.freq = self.freqMin

        # NOW just setting these pins to GND via wires, instead of using up ports
        # # set ms1/ms2 pins to gnd to do 8 microsteps
        # self._pinMs1 = digitalio.DigitalInOut(self._pinMs1Pin)
        # self._pinMs1.direction = digitalio.Direction.OUTPUT
        # self._pinMs1.value = False #GND
        # # self._pinMs1.pull = digitalio.Pull.DOWN
        # self._pinMs2 = digitalio.DigitalInOut(self._pinMs2Pin)
        # self._pinMs2.direction = digitalio.Direction.OUTPUT
        # self._pinMs2.value = False #GND
        # # self._pinMs2.pull = digitalio.Pull.DOWN

        # ensure disabled since GND=on and default state of pin is GND, thus drive would be on
        self.disable()

        # ensure fwd
        self.fwd()

        # For our async spin method, let's create a boolean that we can watch
        # so if it becomes True, we can exit the async process
        self._isAsyncSpinning = False

        # print vals of pins on init
        self.dump()

        # setup a time.monotonic() so our diag check doesn't error out
        self._lastTimeDiagShown = time.time()

    def dump(self):
        # print vals of pins on init
        print("---Elevator DUMP----")
        print("Enable:", self._pinEnable.value)
        print("Dir:", self._pinDir.value)
        print("Step: Freq:", self._pinStep.frequency, "Duty:", self._pinStep.duty_cycle)
        print("Diag:", self._pinDiag.value)
        # print("MS1:", self._pinMs1.value)
        # print("MS2:", self._pinMs2.value)
        print("-------")

    def step(self):
        
        # print("Stepping...")
        self._pinStep.value = True
        time.sleep(self._minPulseWidth)
        self._pinStep.value = False
        time.sleep(self._minPulseWidth)

    def steps(self, cnt):
        print("Stepping", cnt, "steps...")
        for i in range(cnt):
            self.step()
        print("Done stepping", cnt, "steps")

    # Do steps, but enable/disable as part of it
    def stepsEnDis(self, cnt):
        self.enable()
        print("Enabling. Stepping", cnt, "steps...")
        for i in range(cnt):
            self.step()
        self.disable()
        print("Disabled. Done stepping", cnt, "steps")

    def enable(self):
        # Enable Motor Outputs (GND=on, VIO=off)
        # enable driver
        self._pinEnable.value = False 
        # self._pinEnable.pull = digitalio.Pull.DOWN
        print("Elevator Enabled")

    def disable(self):
        # Enable Motor Outputs (GND=on, VIO=off)
        # enable driver
        self._pinEnable.value = True 
        # self._pinEnable.pull = digitalio.Pull.UP
        print("Elevator Disabled")

    def fwd(self):
        print("Elevator Going fwd")
        self._pinDir.value = True

    def rev(self):
        print("Elevator Going rev")
        self._pinDir.value = False

    def setMinPulseWidth(self, seconds):
        print("Set min pulse width:", seconds)
        self._minPulseWidth = seconds

    def deinit(self):
        self._pinEnable.deinit()
        self._pinDir.deinit()
        self._pinStep.deinit()
        self._pinDiag.deinit()
        # self._pinMs1.deinit()
        # self._pinMs2.deinit()
        print("Elevator Deinitted")

    def spinAsyncStop(self):
        self._isAsyncSpinning = False

    def spinAsyncStart(self):
        self._isAsyncSpinning = True

    def setState(self, state:StepperState):
        """Tell us what state you're setting and we will produce the callbacks if there
        was a change of state."""

        lastState = self.state

        # Set our state
        self.state = state

        if state != lastState:
            # We have a state change
            # Call the callback
            if state == StepperState.ACCELERATING:
                if self.onAccelCb != None: self.onAccelCb()
            elif state == StepperState.MAXSPEED:
                if self.onMaxSpeedCb != None: self.onMaxSpeedCb()
            elif state == StepperState.DECELERATING:
                if self.onDecelCb != None: self.onDecelCb()
            elif state == StepperState.STOPPED:
                if self.onStoppedCb != None: self.onStoppedCb()
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

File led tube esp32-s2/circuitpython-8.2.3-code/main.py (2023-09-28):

import time
import touchio
import board
import asyncio
import microcontroller
import neopixel
import supervisor

class Main:
    def __init__(self):

        print("Initting main code")

        # How many touch sensors. They must be in contiguous order starting at Touch1, i.e. board.IO1
        self.numTouchSensors = 14

        # This is threshold for the touch sensors whereby if the raw_value
        # goes above the configured value on boot up, it triggers a touch
        # The default is 100
        self.threshold = 100 

        # Base brightness of blue color that shows across whole strip while idel
        self.baseBlue = 5
        
        # We will create the task later in the process
        self.touch_watcher_task = None # asyncio.create_task(self.asyncTouchWatcherTask())

        # Setup LEDs
        pixel_pin = board.IO21
        self.num_pixels = 28

        self.pixels = neopixel.NeoPixel(pixel_pin, self.num_pixels, brightness=1.0, auto_write=False, pixel_order=neopixel.GRB)

        self.RED = (255, 0, 0)
        self.YELLOW = (255, 150, 0)
        self.GREEN = (0, 255, 0)
        self.CYAN = (0, 255, 255)
        self.BLUE = (0, 0, 255)
        self.PURPLE = (180, 0, 255)
        self.BLACK = (0, 0, 0)

        

        # Run a color cycle startup sequence
        # self.color_cycle_task = asyncio.create_task(self.asyncRainbowCycleTask())

        # Create an async timer that reboots the ESP32-S2 every 8 hours
        # self.reboot_timer_task = asyncio.create_task(self.rebootTimer(20))  # 1 minute for testing
        self.reboot_timer_task = asyncio.create_task(self.rebootTimer(60*60*8)) # 8 hours
        
    def runStartupColors(self):

        pass

    def wheel(self, pos):
        
        # Input a value 0 to 255 to get a color value.
        # The colours are a transition r - g - b - back to r.
        
        # print("pos:", pos)

        if pos < 0 or pos > 255:
            r = g = b = 0
        elif pos < 85:
            r = int(pos * 3)
            g = int(255 - pos * 3)
            b = 0
        elif pos < 170:
            pos -= 85
            r = int(255 - pos * 3)
            g = 0
            b = int(pos * 3)
        else:
            pos -= 170
            r = 0
            g = int(pos * 3)
            b = int(255 - pos * 3)
        return (r, g, b) #if self.ORDER in (neopixel.RGB, neopixel.GRB) else (r, g, b, 0)


    async def asyncRainbowCycleTask(self):
        
        print("Starting rainbow cycle")
        
        # Do an async version of color cycling
        
        # Run 10 times
        for numLoops in range(1):
            
            print("Loop", numLoops)

            for j in range(0, 255, 10):
                # print("In rainbow cycle. j:", j)
                self.pixels.brightness = 1.0
                for i in range(self.num_pixels):
                    pixel_index = (i * 256 // self.num_pixels) + j
                    self.pixels[i] = self.wheel(pixel_index & 255)
                self.pixels.show()
                
                # sleep 0.01 second per loop 
                await asyncio.sleep(0.00000)

        print("Done running rainbow cycle")

    def dumpAllThresholdVals(self):
        
        for i in range(self.numTouchSensors):
            print("Touch", i+1, ", Raw:", self.touch[i].raw_value, "Thresh:", self.touch[i].threshold)

    def setupTouchButtons(self):
        
        print("Setting up touch buttons...")

        # Setup touch buttons
        self.touch = []
        for i in range(14):
            # self.touch.append(1) 
            pinStr = "board.IO" + str(i+1)
            print("Creating touch pin:", pinStr)
            self.touch.append(
                touchio.TouchIn(eval(pinStr))
            )

            # Set threshold lower than the default 100 for each one
            # So remove the 100 that Adafruit added, then add our own
            self.touch[i].threshold = self.touch[i].threshold - 100 + self.threshold
       
    async def runThresholdTest(self):

        # We are going to run a test where we keep track of the max, min, avg, numSamples of each
        # of the 14 touch sensors
        
        d = []

        for i in range(self.numTouchSensors):

            # create data entry
            d.append({
                "min": None,
                "max": None,
                "runTot": None,
                "numSamples": 0
            })

            # print prev test
            if i > 0:
                print("d[" + str(i-1) + "]", d[i-1])

            for testCtr in range(10):
                # run 10 tests
                raw = self.touch[i].raw_value
                
                # see if first time thru
                print("i:", i, "testCtr:", testCtr, "raw:", raw, "raw_value:", self.touch[i].raw_value)
                if d[i]["min"] == None:
                    # it is first time thru, so just set raw to all min, max, and avg
                    d[i]["min"] = d[i]["max"] = d[i]["runTot"] = raw

                else:

                    if raw < d[i]["min"]:
                        d[i]["min"] = raw

                    if raw > d[i]["max"]:
                        d[i]["max"] = raw

                    # set avg
                    d[i]["runTot"] += raw

                d[i]["numSamples"] += 1

                await asyncio.sleep(0.5)
                # time.sleep(0.5)

        # Now dump test
        print("Indx", "Min", "Max", "RunTot", "Avg", "NumSamp")
        for i in range(self.numTouchSensors):
            print(i, d[i]["min"], d[i]["max"], d[i]["runTot"], 0,  d[i]["numSamples"])

    def showGreenLeds(self):

        self.pixels.fill(self.GREEN)
        self.pixels.show()

    def showRedLeds(self):

        self.pixels.fill(self.RED)
        self.pixels.show()

    def showPurpleLeds(self):

        self.pixels.fill(self.PURPLE)
        self.pixels.show()

    def show2YellowLeds(self):

        self.pixels[0] = self.YELLOW
        self.pixels[27] = self.YELLOW
        self.pixels.show()

    async def asyncTouchWatcherTask(self):
        print("Starting infinite async touch watcher loop")

        self.pixels.fill((0,0,self.baseBlue))
        self.pixels.show()

        # The amount of color in each of the rgb to decrement each time thru loop if touch is not present
        # This means if there was a prior touch you'll get a slow fade from the original full brightness on
        # those particular pixels
        decrementPerStep = 3

        # Define our dirty var so it's not instantiated each time thru loop
        # this is for extra loop speed
        isDirty = False 

        # keep track of a loop counter just so we can see how fast we're looping
        # i.e. are we achieving our expected rate
        loopCtr = 0

        dirtyCtr = 0
        triggerCtr = 0
        
        while True:

            loopCtr += 1
            
            # print("In touch watcher async loop, checking on touch state...")
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

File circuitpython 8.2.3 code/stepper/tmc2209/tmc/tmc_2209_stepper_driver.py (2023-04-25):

from .tmc_2209_uart import TMC_UART
from . import tmc_2209_reg as reg
from board import Pin as GPIO
import board
import time
import math

class Direction():
    CCW = 0
    CW = 1

class Loglevel():
    none = 0
    error = 10
    info = 20
    debug = 30
    movement = 40
    all = 100

class MovementAbsRel():
    absolute = 0
    relative = 1

#-----------------------------------------------------------------------
# TMC_2209
#
# this class has two different functions:
# 1. change setting in the TMC-driver via UART
# 2. move the motor via STEP/DIR pins
#-----------------------------------------------------------------------
class TMC_2209:
    
    tmc_uart = None
    _pin_step = -1
    _pin_dir = -1
    _pin_en = -1
    p_pin_step = -1
    p_pin_dir = -1
    p_pin_en = -1
    
    _direction = True

    _stop = False

    _msres = -1
    _stepsPerRevolution = 0
    
    _loglevel = Loglevel.none

    _currentPos = 0                 # current position of stepper in steps
    _targetPos = 0                  # the target position in steps
    _speed = 0.0                    # the current speed in steps per second
    _maxSpeed = 1.0                 # the maximum speed in steps per second
    _maxSpeedHoming = 500           # the maximum speed in steps per second for homing
    _acceleration = 1.0             # the acceleration in steps per second per second
    _accelerationHoming = 10000     # the acceleration in steps per second per second for homing
    _sqrt_twoa = 1.0                # Precomputed sqrt(2*_acceleration)
    _stepInterval = 0               # the current interval between two steps
    _minPulseWidth = 1              # minimum allowed pulse with in microseconds
    _lastStepTime = 0               # The last step time in microseconds
    _n = 0                          # step counter
    _c0 = 0                         # Initial step size in microseconds
    _cn = 0                         # Last step size in microseconds
    _cmin = 0                       # Min step size in microseconds based on maxSpeed
    _sg_threshold = 100             # threshold for stallguard
    _movement_abs_rel = MovementAbsRel.absolute
    
    def mean(obj, x):
        a = 0
        for v in x:
           a=a+v
        return(a/len(x))

#-----------------------------------------------------------------------
# constructor
#-----------------------------------------------------------------------
    def __init__(self, pin_step, pin_dir, pin_en, baudrate=115200, serialport=2):
        
        self.tmc_uart = TMC_UART(serialport, baudrate)
        self._pin_step = pin_step
        self._pin_dir = pin_dir
        self._pin_en = pin_en
        if(self._loglevel >= Loglevel.info):
            print("TMC2209: Init")
        self.p_pin_step = GPIO(self._pin_step, GPIO.OUT)
        self.p_pin_dir = GPIO(self._pin_dir, GPIO.OUT)
        self.p_pin_en = GPIO(self._pin_en, GPIO.OUT)
        self.p_pin_dir(self._direction)
        if(self._loglevel >= Loglevel.info):
            print("TMC2209: GPIO Init finished")      
        self.readStepsPerRevolution()
        self.clearGSTAT()
        self.tmc_uart.flushSerialBuffer()
        if(self._loglevel >= Loglevel.info):
            print("TMC2209: Init finished")


#-----------------------------------------------------------------------
# destructor
#-----------------------------------------------------------------------
    def __del__(self):
        if(self._loglevel >= Loglevel.info):
            print("TMC2209: Deinit")
        self.setMotorEnabled(False)
        GPIO.cleanup() 

#-----------------------------------------------------------------------
# set the loglevel. See the Enum Loglevel
#-----------------------------------------------------------------------       
    def setLoglevel(self, loglevel):
        self._loglevel = loglevel

#-----------------------------------------------------------------------
# set whether the movment should be relative or absolute by default.
# See the Enum MovementAbsoluteRelative
#-----------------------------------------------------------------------       
    def setMovementAbsRel(self, movement_abs_rel):
        self._movement_abs_rel = movement_abs_rel

#-----------------------------------------------------------------------
# read the register Adress "DRVSTATUS" and prints all current setting
#-----------------------------------------------------------------------
    def readDRVSTATUS(self):
        print("TMC2209: ---")
        print("TMC2209: DRIVER STATUS:")
        drvstatus =self.tmc_uart.read_int(reg.DRVSTATUS)
        if(self._loglevel >= Loglevel.info):
            print("TMC2209:", bin(drvstatus))
        if(drvstatus & reg.stst):
            print("TMC2209: Info: motor is standing still")
        else:
            print("TMC2209: Info: motor is running")

        if(drvstatus & reg.stealth):
            print("TMC2209: Info: motor is running on StealthChop")
        else:
            print("TMC2209: Info: motor is running on SpreadCycle")

        cs_actual = drvstatus & reg.cs_actual
        cs_actual = cs_actual >> 16
        print("TMC2209: CS actual: "+str(cs_actual))

        if(drvstatus & reg.olb):
            print("TMC2209: Warning: Open load detected on phase B")
        
        if(drvstatus & reg.ola):
            print("TMC2209: Warning: Open load detected on phase A")
        
        if(drvstatus & reg.s2vsb):
            print("TMC2209: Error: Short on low-side MOSFET detected on phase B. The driver becomes disabled")

        if(drvstatus & reg.s2vsa):
            print("TMC2209: Error: Short on low-side MOSFET detected on phase A. The driver becomes disabled")

        if(drvstatus & reg.s2gb):
            print("TMC2209: Error: Short to GND detected on phase B. The driver becomes disabled. ")
        
        if(drvstatus & reg.s2ga):
            print("TMC2209: Error: Short to GND detected on phase A. The driver becomes disabled. ")
        
        if(drvstatus & reg.ot):
            print("TMC2209: Error: Driver Overheating!")
        
        if(drvstatus & reg.otpw):
            print("TMC2209: Warning: Driver Overheating Prewarning!")
        
        print("---")
        return drvstatus
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

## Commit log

2023-04-25 Move circuitpython code to folder
2023-04-25 Add Fusion360 and STLs
    [1stAngleWithWallBracket.3mf, 1stGear10Teeth12mmWide.3mf, 1stGearCap.3mf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]
2023-05-06 Final version
    [136DegreeAngleWithWallBracket.3mf, AcrylicFrontCoverOfPCBBox_LaserCut.dxf, BtnHolder.3mf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]
2023-08-17 Created 8.2.3 code so no crashing
    and motor turned off when idle
    [button.py, button_mimic.py, counter.py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]
2023-08-17 Latest 3mfs and cad
    [1stGear10Teeth12mmWide8mmShaftHole.3mf, 2ndGear18Teeth12mmWide.3mf, 2ndGearInnerAxleCap.3mf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]
2023-08-17 New 3mfs for pipe system
    [BracketToWall12Magnets.3mf, BracketToWall15Deg.3mf, BracketToWall15Magnets.3mf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]
2023-08-18 Enahnced pipe system
    [BracketToWall12Magnets24mm.3mf, BracketToWall15Deg.3mf, BracketToWall15Magnets30mm.3mf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]
2023-08-18 Removed old designs
    [30DegWindowTubev3-0.2mmShavedOffRail.3mf, BracketToWall12Magnets.3mf, BracketToWall15Magnets.3mf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]
2023-08-18 New tube lengths 5, 10, 20
    [Tube10mm.3mf, Tube20mm.3mf, Tube5mm.3mf]
2023-08-21 LED Tube
2023-08-21 Changed folder name
    [1stGear10Teeth12mmWide8mmShaftHole.3mf, 2ndGear18Teeth12mmWide.3mf, 2ndGearInnerAxleCap.3mf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]
2023-08-21 Latest tubes and cad
    [BracketToWall12Magnets24mm.3mf, BracketToWall15Deg.3mf, BracketToWall15Magnets30mm.3mf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]
2023-08-22 New 3mfs and cad
    [Bambu_NewTubesAug21_2023.3mf, BracketToWall15Deg.3mf, BracketToWall30Deg.3mf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]
2023-08-22 Latest LED Tube
